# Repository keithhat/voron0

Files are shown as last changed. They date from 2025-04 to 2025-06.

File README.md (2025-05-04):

# voron0
This tracks my Voron 0 build.
This was originally a Siboor 0.2 r1 kit (Aug2023) with ABS printed parts. I bought of AliExpress from official Siboor retailer.
Having time again I'd see price bying from siboor directly to choose different colours.

# Main Info
* http://192.168.7.60/#/ (Ethernet)
	* WiFi 2.4GHz: http://192.168.7.61/#/
* Login:
	* username: fly
	* default password: mellow
* I bought this kit: https://www.aliexpress.com/item/1005005295642824.html
	* When purchased I got with Drafon HF Hotend and Red ABS parts for AUD 943.02 (with shipping).
	* As at 2025-05-01 it is: AUD 645.39 with no ABS and TZ-V6-2.0 (if wanted second...)
* Siboor has a collection of useful links: https://docs.siboor.com/welcome-to-siboor/friendly-links

# Notes
* Do NOT do full apt upgrade on console.
	* I initially broke my Siboor image doing this, I did force some which may have been kernal.
	* I got everything back using Gemini images and some sample Siboor files.
	* Updating through the mainsail interface was ok, including plugins. Some had path clashes that were easily resolved.
* The polarity of at least the extruder fan is important.
* My extruder was skipping when initially tuning, ended up being some broken filament in heatbreak. Disassembled and used a tool to help extract
* It was originally not clear to me, but the z-axis should be configured so toolhead is at 0.0 for correct printing location. (I originally had bottom as 0 and this at 120).

# Build Info
## Mechanical Assembly
* The mechanical build largely went well following the PDF manuals.
	* As this was a 0.2r1 kit some mod 'patches' were not fully covered.
* Main Manuals and Notes during mechanical assembly (in assembly folder):
	* [BuildNotes.md](assembly/BuildNotes.md) these are verbose notes /ideas while mechically building device
	* 0 Keith Notes.txt - this was intended as concise patches to readme and assembly manual
	* 1 README with deltas to official was originally from: https://github.com/Lzhikai/SIBOOR-Voron-0.2/blob/main/supplementary/README.md
  	* 2 Official 0.2 Assembly Manual was originlly from: https://github.com/VoronDesign/Voron-0/blob/Voron0.2/Manuals/VORON_V0.2_Assembly_Manual.pdf
  	* 3 Siboor Supplementary with info on Motors and Feet was originally from: https://github.com/Lzhikai/SIBOOR-Voron-0.2/blob/main/supplementary/SIBOOR%20V0.2%20Supplementary%20Manual.pdf
  	* 4 Siboor Supplementary with info on Wiring / Motors was originally from: https://github.com/Lzhikai/SIBOOR-Voron-0.2/blob/main/supplementary/SIBOOR0.2-supplementary.pdf
  	* 5 Siboor Upgrades was originally from: https://github.com/Lzhikai/SIBOOR-Voron-0.2/blob/main/supplementary/SIBOOR%200.2%20R0%20Upgrade%20R1%20Guide.pdf
 * Other Info:
  	* Siboor V0.2 Bom: https://github.com/Lzhikai/SIBOOR-Voron-0.2/blob/main/BOM.md
	* Root Project from QR Code: https://github.com/Lzhikai/siboor-voron/tree/main/Voron-0.2
* During assembly I originally missed the rear-right foot with bowden collet and run-out sensor.
	* This was created from the Siboor screenshot and required hardware in [RearRightFoot.jpg](images/R1_Rear_Right_Foot/RearRightFoot.jpg) (I only used 1 M2x10)
* The ADX345 accelerometer mounting was eventually found at end of "assembly/4 SIBOOR0.2-supplementary.pdf".
	* I had previouslly used longer bolts and attempt to mount to front of toolhead.
## Electrical
My extruder fan was not originally working. This was tracked to a polarity issue into the fan cable. These cannot be swapped.

## FW
(!)Do not do arbitrary system udpates for gemini board. Updating through mainsail interface was ok though.
Flashing fimware main indicate success and failure; this was found to be ok but confirmed through dfinding id

# Current Main Components
* Kirigami Bed
	* Has 8 RGB LED neopixel in logo
* Phaetus Dragon HF Hotend
* Gemini v3 mainboard
* V0 Umbilical
	* This is fairly stiff; a CAM bus or USB equivalent think would be useful in future

# Guides - Assembly, FW and Tuning
## General
* Siboor v0.2 r1 Aug: https://docs.siboor.com/siboor-0.2-r1-aug
	* Initial Startup and Wiring: https://docs.siboor.com/siboor-0.2-r1-aug/the-build/initial-startup
	* Mods to vanilla: https://docs.siboor.com/siboor-0.2-r1-aug/the-build/assembly-manual
* Gemini v3:
	* Image: https://mellow.klipper.cn/en/docs/ResDownload/system-img/fly-Gemini/?persistLocale=true
	* General: https://mellow-3d.github.io/fly-gemini_v3_general.html
	* Fan: https://mellow.klipper.cn/en/docs/ProductDoc/MainBoard/fly-gemini/fly-gemini-v3/fan/
* Voron: https://docs.vorondesign.com/build/software/

## Tuning and Initial Setup
This explicitly calls out some sections
* I missed it originally, but want to end up having z=0 (z0) being where the toolhead needs to be to touch plate and be ready for printing. We adjust Z switch so this is true.
	* See https://docs.vorondesign.com/build/startup/#stepper-motor-check and matching video: https://www.youtube.com/watch?v=wXYruV6QdDQ$t=1700
* Moving, homing, estep, PID: https://docs.vorondesign.com/build/startup/
	* Sensorless Homing: https://docs.vorondesign.com/tuning/sensorless.html
	* A video of these is: https://www.youtube.com/watch?v=wXYruV6QdDQ
* Klipper Common Errors: https://docs.vorondesign.com/community/troubleshooting/eddie/klipper_common_errors.html

## Sample Configus
* Siboor Voron 0.2 Aug: https://github.com/Lzhikai/SIBOOR-Voron-0.2-AUG/blob/main/printer.cfg

## Neopixel
0.2 Kirigami bed has a neopixel LED that can have effects. This can be used with 2xLED strips as 'Disco on a Stick' with wiring shown at [DaisyChain Neopixel RGBs](images/02_LED_Wiring/Multiple_RGBs.jpg)

### LED effects
* https://github.com/julianschill/klipper-led_effect
* https://docs.siboor.com/other-products/led-effect-notes/configuring-the-effects
* https://docs.siboor.com/other-products/led-effect-notes/advanced-effect-layer-blending

### Various Sample Effects
* https://gist.github.com/bistory/08e279ebda4d5cd2521dfe1add09dab4
* https://pastebin.com/GBzkNXcq
* https://pastebin.com/pv8M4huD
* https://github.com/julianschill/klipper-led_effect/blob/master/examples/Voron_Stealthburner/stealthburner_led_effects_3_leds.cfg

## Ultimaker Cura Integration
* I followed the guide at: [3 Siboor v0.2 Supplementary Manual](https://github.com/Lzhikai/SIBOOR-Voron-0.2/blob/main/supplementary/SIBOOR%20V0.2%20Supplementary%20Manual.pdf)
	* Same info in [4 Siboor0.2-Supplementary.pdf](https://github.com/Lzhikai/SIBOOR-Voron-0.2/blob/main/supplementary/SIBOOR0.2-supplementary.pdf)

## Unsure if used:
* https://www.klipper3d.org/Config_Reference.html

# Additional Purchases:

## Parts for physical assembly (also in [BuildNotes.md](assembly/BuildNotes.md))
* Isopropyl alchohol
* WD40 White Lithium Greece (spray can)
    * I used as lubricate for linear rails and screw
* Permatex White Lithium Grease - 80345 for bearings
    * For print head bearings
* Locktight Blue for grub screws
* Super glue for print head nut
    * I had 2 part 5min eproxy
* Cable cutter and stripper
* JST XH connector tool - at least for hotend to Umbiligal PCB
* Optional:
    * Cable management stickies

## Tools post-assembly
The Dragon HF seemed to be missing some additional tools in full kit; ended up getting the following to help
I bought following:
* Open Ended Mini Spanners: https://www.amazon.com.au/dp/B0DBY93B7Q 			AUD 14.98 	Set (4mm, 4.5, 5, 5.5, 6, 7, 8, 9, 10, 11)
    * These worked for removing nozzel from Dragon HF, but was relatively thick for disassembly heatbreak from heat-block.
* Hex Wrench for Dragon HF heat-block (1.27mm):
	* https://www.ebay.com.au/itm/196192220714 AUD 24.88 for Set (0.9, 1.27, 1.3, 1.5, 2.0)
	* https://www.ebay.com.au/itm/134291755243 AUD 3.10 single 1.27mm
* Hex multi-tool to help with Hotend: https://www.amazon.com.au/dp/B0DSBQDLFP 	AUD 11.89 	Spanner: (6, 7, 8, 10,20), Hex Tool: (M2.5, M2, M3, M4), Copper Wire Brush
	* Got to help have a thinner spanner for Dragon HF disassembly - unblocked before needing to disassemble.
* Filament unblock tool (when nozel removed): https://www.aliexpress.com/item/1005002948629438.html 	AUD 2.95
	* I made a seperate heatbreak and heat block that could be connected to umbilical and moved from printer to help unblock.
		* Heater Block: https://www.aliexpress.com/item/1005005038625574.html 	AU 8.99 	Up to 500deg. Missing silicon sock, I got the wrong one.
* Nozzle Needless:
	* https://www.aliexpress.com/item/1005004227280655.html AUD 4.09 	(0.2 and 0.5)
* Anti-Static Tweezer set: https://www.aliexpress.com/item/1005007425589207.html 	AU 4.59

# Additional Parts
## General
These can be ued with several of below
* I bought several hardened steel nozels for different sizes and abrasive materials.:
	* https://www.aliexpress.com/item/1005001620042630.html 	AUD 4.14  	I got pairs on: (0.2, 0.4, 0.6)
* Drive Gear with Hardended Steel gears - have NOT yet used this for gears (arrived after re-assembling mini Stealthburner)
	* https://www.aliexpress.com/item/1005007929025658.html 	AU 7.39 	Intended as spare 50T gear and abrasiev filamenets.
* Adapter for screen USB Cable
	* This seemed tight against sides; didn't want to damage the screen cable so got something else to prolong life.
	* Tried a few 90deg adapters but either blocked ports or didn't have clearance.
	* Currently using a USB A 30cm extension cable: https://www.ebay.com.au/itm/135236859084 AU 4.95
* Small Camera:
	* USB 'RPI 3 Model B 640x480' https://www.amazon.com.au/dp/B09KHHN8B3 	AU 13.26 Not yet working; unsure if HW/SW/Drivers

## Parts for Dragon HF Hotend abrasive/replacement
These are not yet used, arrived too late. 
TODO: Need silicon cover. This is WRONG for Phaetus Dragon HF: https://www.aliexpress.com/item/1005005886011113.html 	AU 5.79
TODO: Need cool zone? Possibly something that can be shared with EnderNG
* I made a hotend that could be used to unblock hotend or nozels (think 3rd party Dragon HF):
	* 50W 24V thermistor / heaterset: https://www.aliexpress.com/item/32967546419.html 	AU 5.39
	* HF Heatbrewak: https://www.aliexpress.com/item/1005006869637598.html 	AU 23.79

## Replacement Hotend
A cheaper hotend for abrasive seems useful. Also allows using if Dragon blocked.
TODO: Confirm can use above hardened steel nozzels
TODO: Make up as drop-in for Dragon HF; mini stealthburner, then Dragon Burner
* I later bought a TZ-V6 2.0 Hotend - 35mm3/s
	* 60W V6: https://www.aliexpress.com/item/1005006417172044.html 	AU35.19. TBC if ok for abrasive.
		* Nozzle: SKD11, hardness: HRC60 - TBC if takes above V6 hardened stell (this looked smaller.)

## Dragon Burner
The Dragon Burner seems to be better reviewed, especially for PLA. Also would like a filament cutter (for box turtle) and nozzle probe for correct z-offset.
Home is: * Dragon Burner v8 Home: https://github.com/chirpy2605/voron/blob/main/V0/Dragon_Burner/README.md

### Bought Parts
* 1x 3010 24V 			https://www.aliexpress.com/item/1005002857100082.html 	AU 13.89 x1
* 2x 4010 Blower 24V 	https://www.aliexpress.com/item/32799324058.html 		AU 9.49 x2
* Orbiter v2.5 Extruder: https://www.aliexpress.com/item/1005007653572332.html 	AU 79.18
* Logo NeoPixel: https://www.aliexpress.com/item/1005006046634379.html 	AU 11.79 	(looks to have sockers already) + 2 LEDs
	* NeoPixel DIY: https://www.aliexpress.com/item/1005007646205279.htm 	AU 6.09 	<- Unsure if would be better than above. Got both to check.
* RGA Sequins: https://www.aliexpress.com/item/1005006023213341.html 	AU 5.62 (4 LEDs)
	* Neopixel Alternative: https://www.aliexpress.com/item/1005006220336798.htm 	AU 5.79 	<- I got both, thought this was neopixel above normal RGB

## Purchases but not necessarily used:
These maybe used on my Ender3 v2 to NG upgrade instead (for larger build volume). Plan to do that AFTER the v0.2 is working so have something working at all times.
* Funssor Ender 3 NG Conversion Kit: https://www.aliexpress.com/item/1005006191089001.html 	AU 188.98 motion and electronics
	* Note bought in 2024 prior to offical release. Maybe newer versions now eg : https://www.aliexpress.com/item/1005007822628611.html Ender NG v1.2 for 290.99 / 326.69 wuth motors
* Klipper expansion board - may need for lights: https://www.aliexpress.com/item/1005005777656355.html 	AU24.99
* Klicky Kit for bed levelling: https://www.aliexpress.com/item/1005005467101449.html 	AU 7.19 	Bought in 2024, maybe better optiosn now
* Nevermore v6 DUO Cabon Filters for Voron: https://www.aliexpress.com/item/1005005621338360.html 	AU 36.05 for 2
* PEI + Smooth PEO Build Plate: https://www.aliexpress.com/item/1005006950525967.html 	AU 11.37
* RGB LEDs: https://www.aliexpress.com/item/1005007075886697.html 	AUD 17.27 for 2x158mm
* Belt Tensionmeter: https://www.aliexpress.com/item/1005006724674386.html 	AU 12.20 (I used guitar tuner while initially building)
* ADXL345 3 Axis Acceleration Module: https://www.aliexpress.com/item/32452794842.html 	AU 5.41 (think kit had some too)
* Filament Run-out sensor: https://www.aliexpress.com/item/32917462715.html 	AU 3.35
* PTFE Tube https://www.aliexpress.com/item/1005004969503645.html 	AU 7.50 for 2m with cutter
* 10ml 243 Loctite: AUD 4.42
* G10 FR4 FibreGlass Sheet (Green PCB Material):
	* Single Sided Copper: https://www.aliexpress.com/item/1005006103130312.html 	AU 4.39 for 120x180 - I have 20x30 for 9.74
	* AU 14.19 for 235x235x1.5mm

# Interesting parts that may help in future
 * [NoDropNuts](https://mods.vorondesign.com/details/XGjXJC3VQU76EBYB7Yg) look interesting
 * [Snap in M3 Nuts for 1515](https://www.printables.com/model/410126-snap-in-m3-nuts-for-makerbeam-xl-1515) - ie for Nevermore

# Future Thoughts
These are tracked in [Future.md](future.md)

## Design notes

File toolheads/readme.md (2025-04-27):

This is tracking my ideas for hotends.
There maybe other info at: https://3dprintersforants.com/

Rough plan is:
	- Have a Dragpn HF in Mini Stealth burner.
		- Want a second Hotend for abrasive materials - also handle blocks
		- MAY want additional parts to help with Dragon HF clogs - think had snapped filament cause this at start

Mini StealthBurner - Default Toolhead

Dragon Burner:
	- https://github.com/chirpy2605/voron/tree/main/V0/Dragon_Burner
		- v8 was defined for Voron 0.2
	- Bom (Extracted)
		- FANS:
			- Part Cooling: 2x 4010 24V blower fans
				- Recommended: https://www.aliexpress.com/item/32799324058.html 	(24V Hydraulic 2PIN) AUD 5.05
			- Hotend Cooling: 1x 3010 24V
				- Recommended: https://www.aliexpress.com/item/1005002857100082.html ( 24V Sleeve 2PIN) AUD $ 12.79
		- LEDs:
			- 3x LEDs for lgoo and nozzle lights (optional)
				- Can be a mixture of NeoPixels and/or Sequins (nozzle??)
				- Support has been added for either standard Neopixels or Sequins for the nozzle LEDs, Neopixels, Sequins and RainbowBarf for the Logo LED.
				- Links I found:
					- https://www.aliexpress.com/item/1005007646205279.html AUD 1.59 (need to solder/crimp myself)
					- https://www.aliexpress.com/item/1005006046634379.htm AUD 10.59 looks socketed prepared for StealthBurner
					- Sequins: https://www.aliexpress.com/item/1005006023213341.html AUD 1.59 - DIY
					- Neopixel Sequins: https://www.aliexpress.com/item/1005006220336798.html AUD 1.83
		Dragon SF and HF
		Dragon + Volcano (Rapido HF mount)
		Dragonfly BMO
		Dragonfly BMS (7 fin)
		Revo Voron
		Rapido HF
		NF Crazy
		Creality Spider Pro
		Bambu Labs X1C
		TaiChi
		E3D V6 Groove Mount
		Red Lizard K1 Pro (Dragon mount)
		Red Lizard K1 UHF (Rapido HF mount)
		Dragon Ace HF (with spacer use the Rapido HF mount, without spacer use the Dragon Ace HF mount)
		Phaetus NeXt G HF (Dragon mount)
		Phaetus NeXt G UHF (Rapido HF mount)
	- Extruder:
		Extruder support:
		E3D Roto Vitamins (use the Sherpa Mini hotend mount)
		LGX Lite (use the Sherpa Mini hotend mount)
		Sherpa Mini
		Sherpa Micro
		Sailfin/Sharkfin
		Orbiter v1.5
		Orbiter v2
		Vz-HextrudORT (Uses the LGX Lite extruder mount and Sherpa Mini hotend mount)
		Double Folded Ascender
		RoundTrip (Gears from the LGX Lite, TBG Lite, Orbiter v1.5, Orbiter v2)
		Galileo v2 Standalone (G2SA) with specific mounts for Sherpa Mini and Orbiter v2 mount hole configurations
		Wristwatch BMG and G2 use the Orbiter v2 hotend mounts
		Papilio Lite (Paplite) extruder (use Sherpa Mini mount)
	- Probes:
		- SlideSwipe magnetic probe support: https://github.com/chestwood96/SlideSwipe - likley start with: https://github.com/chestwood96/SlideSwipe/blob/master/Alternative_Mounts/FrontCowlingMount/README.md
		- (Un)Klicky Probe support: https://github.com/jlas1/Klicky-Probe/tree/main/Printers/Voron/v0 (also read https://github.com/T4KUUY4/Voron-Stuff/tree/main/KlickyProbeZoffset)
			- https://github.com/jlas1/Klicky-Probe/tree/main/Printers/Voron/v0#integrated-cowling-v01
			- https://github.com/jlas1/Klicky-Probe/tree/main/Probes/KlickyNG
		- ZeroClick probe support: Inspired by Clikcy but for small printers: https://github.com/zruncho3d/ZeroClick
		- Think also Tap and Boop in mounts
	- Mounts:
		- Extruder and PCB Mounts: https://github.com/chirpy2605/voron/tree/main/general/PCB_Mounts
		- Alternative Mounts: Mounts are available
	- Extra:
		- ADXL345 front mount
		- Heatsink thermistor support on most hotend mounts
		- Neopixel support (nozzle and logo)
		- Adafruit Sequin support (nozzle and logo)
		- [Lab4450](Shop - RGB Neopixel Sequins for Voron Mini SB - Lab4450.com) Neopixel Sequin support (nozzle and logo)
			- https://lab4450.com/product/rgb-neopixel-sequins/ EU 2.00
			- https://github.com/julianschill/klipper-led_effect

Noet:
	- Avoid XoL

Want:
	- Dragon HF
	- V6 PZ
	- Orbiter v2.5++

Stetech:
	- Filament Cutter (for AMS)
	- Probe:
		- TAP: https://github.com/chirpy2605/voron/tree/main/general/Alternative_Voron_Mounts/Modified_Mounts/Tap
	- Vooron Revo (ideally with PZ)
		- MAYBE easier to clear clogs;
			- Possibly something else to heatup outside of printer

Future:
	-CAM Bus

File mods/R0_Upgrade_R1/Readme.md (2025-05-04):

# README.MD

These are the Siboor R1 STL Updates
They were downloaded from: https://github.com/Lzhikai/SIBOOR-Voron-0.2/tree/main/supplementary/R0_Upgrade_R1-STL

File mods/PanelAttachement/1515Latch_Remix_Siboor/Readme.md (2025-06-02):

This is from: https://www.printables.com/model/512829-voron-0-filament-latch-remix-for-no-drop-nuts-sibo/files
	- It is remixed of the LDO motors version https://www.printables.com/model/172427-voron-01-filament-latch-1515-extrusion which was based off 2.4 2020 version: https://github.com/richardjm/voron-parts/tree/main/voron-2.4/FilamentLatch

Note:
	- There are two versions here:
		- Short lengths - work with NUT in Siboor/Makerbeam 
		- Stub for no drop nuts
	- Use two per panel edge so 8 for left and 8 for right
		- Maybe spacers for middle of each
	- Door cam ise as a latch

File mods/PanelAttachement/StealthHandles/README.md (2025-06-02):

Source: https://mods.vorondesign.com/details/GHaVestXfFM0svkcJRpk2A

# V0 Stealth Handles

Stealthy and stylish handles for your Voron V0

These handles replace the top center panel clips, and fasten with M3x12 screws.

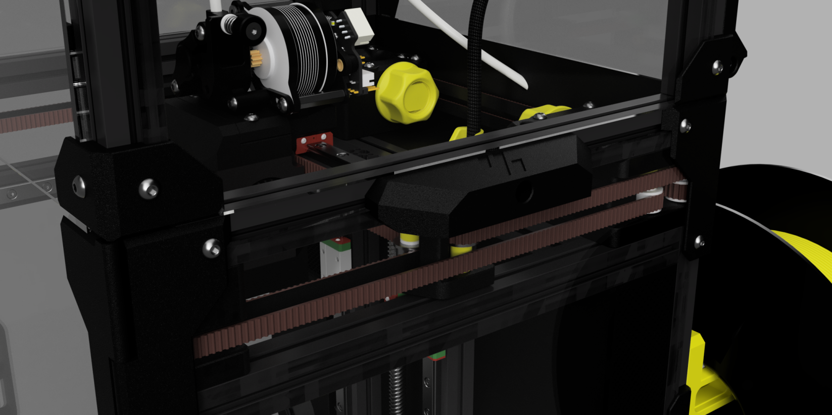
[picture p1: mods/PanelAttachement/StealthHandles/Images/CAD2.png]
CAD2


## Printing

The STL files are already oriented for printing.  No supports are required.  Yes, they print at a 45 degree angle, for some extra strength.

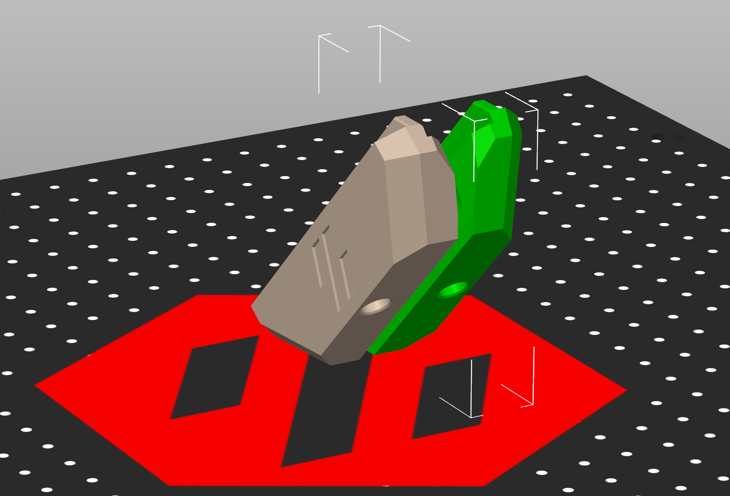
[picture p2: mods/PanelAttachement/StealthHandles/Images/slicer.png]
Slicer


## Changelog

2023-08-24 - Slim down the tabs by 0.2mm for a better fit with some extrusions.

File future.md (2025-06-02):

# Backlog of tasks

This is a backlog of tasks I'd like to improve. It was started after initial mechanical assembly.

# Current Status

## Final setup before doing generic prints

* Calibration Prints
  * cube https://docs.siboor.com/siboor-0.2-r1-aug/the-build/slicer-setup#slice-the-3d-model
  * Initial observations:
      * First layer indicated some issues with oozing; at leat the white filament. Moving from purge line; and first layer
        * Think this is mainly retraction; think a stringing test to help set
      * >>> Have seen layer shits; not always reproduced so see if cause <<< Belt tension, speed etc
      * Klipper console log showed some details - unknown command:
        * Unknown Command:
        *   EXCLUDE_OBJECT_DEFINE - at start
        *   EXCLUDE_OBJECT_START - lots of pairs
        *   EXCLUDE_OBJECT_END 0 lost of pairs
        * Popup at end of Job: Move out of Range: 230 230 36 [7355.028]
      * Some lines shown; seem consistent (for same job); are around end of z etc so maybe not just fixed x cm issues.
      * Annoying; sometimes fails saying neded to home first (after pre-heats bed)
        * This MAYBE intermittent?
  * Assume Will Need:
    * Look for a spool holder incase caused layer shifts - MAYVE poorly mounted originally (using E3 for now)
    * Look at flow rates for material - load filament FAST for ABS resulted in skips towards the end
    * Temperature Tower
    * Retraction Distance - Is this related to oozing??
    * First Layer??
    * Max Dimensions; especially Z and no shifts
    * Anything to help tune acceleration?
  * Maybe more at: https://docs.siboor.com/siboor-0.2-r1-aug/tuning-guides (some of these are below in stretch)
  * Teching Tech or makers muse likely have others; retraction, overhangs etc
* Move printer to next to ender3

## Nice to Have
* Filament runout sensor - from foot
* Look at accelerometer and input shaping.
  * Resonances: https://docs.siboor.com/siboor-0.2-r1-aug/tuning-guides/measuring-resonances
* Check if need to tune: Pressure Advance, Smooth Time
  * Pressure Advance: https://docs.siboor.com/siboor-0.2-r1-aug/tuning-guides/pressure-advance
  * Sameple videos: https://www.youtube.com/watch?v=deqJTNmnVyc  https://www.youtube.com/watch?v=LVp15eGXwm0

## Assistance for maintenance
* Case clips for panel quick attach/detach.
  * Several potential options; check all for V0.2 rather than V2.4 etc
    * Snap Latch for 1515: https://www.printables.com/model/172427-voron-01-filament-latch-1515-extrusion
      * As have M3 nuts MAYBE look at these. Unsure if other remixes etc
    * [FT Panel Clips for Voron V0/V0.1/V0.2] (https://www.printables.com/model/933648-ft-panel-clips-for-voron-v0v01v02) Only negative is key isn't flush
      * Alternative with same idea; https://github.com/KayosMaker/1515PanelClips (based on Annex but no longer skeletonized)
    * Potentially best magnet idea: https://www.printables.com/model/435407-voron-magnetic-panel-clips/comments
      * Unsure if need something else for doors
    * Zero Panels: https://github.com/zruncho3d/ZeroPanels
      * v3 Has tape mainly to keep alignment; potentially would like a version 2 without?
      * Some remix: https://github.com/adooze/ZeroPanels_for_Stock_V0.2
    * Excessively Magnetic Panel Mod https://www.reddit.com/r/VORONDesign/comments/1ccbihw/the_excessively_magnetic_panel_mod_emp_is_now_in/ / 
      * Needs 236x 6x3mm Magents, 8x M3x8 screens, 69xNits and VHB tape
      * Similar (unsure what are best):
        * https://github.com/VoronDesign/VoronUsers/tree/main/printer_mods/bobbleheed/Magnetic_Panels / https://mods.vorondesign.com/details/xQAsIUzijkbXU2yXrRKdXg
* Door handle fix - I'm ok to screw through front panel
  * Randome link: https://mods.vorondesign.com/details/mbzWlsb9PXA54FhWXtRCQ
* Add panels for dust etc
* MAYBE a nozzle cleaner? Lots of ozzing atm. Especially want if using nozzle probe
* Belt Tesnsion checking
  * https://github.com/Diyshift/3D-Printer/tree/main/GT2%20Belt%20Tension%20Meter
    * Need Spring and Piano wiring for correction tension
    * Video of demo: https://www.youtube.com/watch?v=AmgCqy7FisE
    * Link has tension guidlines: 1.9 for Voron 0. When printhead centered (and motors active)

## MVP Completion
* Look at process to apply for serial.

## Stretch

* LED Strips and possibly affects (if RGB)
    * Wiring: https://docs.siboor.com/siboor-0.2-r1-aug/faq-oct-3 
    * https://docs.siboor.com/other-products/led-effect-notes
    * https://docs.siboor.com/other-products/rgb-pcb-light
    * Also some Daylight STLs to mount
* Klipper LED as status - Something for Printing (percentage); loading job? Pause
    * Really want:
      * toolhead neopixel; so can indicate temperate
      * Enclosure LEDs; help show status?
* Camera - mount on top of z extruction.
    * I bought: https://www.amazon.com.au/dp/B09KHHN8B3
      * Look at designing own back mount to replace clip; USB strain relieft MAY need looking at; don't want to resolder anything when swap
      * I broke the retraction (spring flew out).

## Nice to improve

* Can extruder fan be controlled? Think also called hotend fan. Mainly for me being in same room :)
    * Ideally off unless extruder > say 40deg. Allows machine to be quieter / always on.
    * According to: https://docs.siboor.com/siboor-0.2-r1-aug/the-build/initial-startup-checks the Hotend fan cannot be controlled.
    * Any spare switch we can use to control?
    * https://docs.vorondesign.com/build/startup/#pid-tune-bed--hotend says Parts cooling to 25% can be done with: M106 S64
    * Eg: SET_FAN_SPEED FAN=Nevermore SPEED=0.7
    * Fly_Gemini_v3 defines:
        * FAN0=PC6,
        * FAN1=PC7,
* Modest Mesh; maybe several options eg: https://www.printables.com/model/407822-voron-v0-modesty-mesh
* Carry Handle

* What is the MCU LED - has the Kirigami LED replaced this?
* Nevermore chamber filter - to help with ABS fumes as know will be in confined space
* Z-Stop - ideally Nozel probe
    * Prefer probe bed accuratly than assume offset - potentially max height issues though. Good to understand why v0.2 moved to bottom?
    * This looks simple/cheap - doesn't allow for different beds though: https://github.com/Polar-Ted/STL-Files/tree/main/V0.1_Its_Not_a_Sexbolt_switch
        * Video is at: https://www.youtube.com/watch?v=bdxmqTDDsMM
    * Expect some options especially if change to DragonBurner - this would allow for differnt beds too.
    * There are now lots of new options possibly for bed leveling/mesh:
      * Beacon/Cartographer (original)
      * Eddy
      * Tap -> Moves entire toolhead so less rigid; BUT has both bed and nozzle.
      * Klacky? - look at
        - Unsure of nap that nozzle pushed on button next to bed. If this then one it picks up probe temporarily
      * BLTough ? unsure if still useful

* Ensure idler cam locks work well with printer hat
* Check toolhead is ok with PLA, may need better cooling. Think Dragon Burner useful and helps with some other options (filament cutter, maybe probe)
    * Can explore other options including CAM controlled for more flexible cambling
    * Consider adding LED lights; I decided to NOT use in original mini StealthBurner build
    * Consider a filament cutter to allow AMS system such as armoured turtle, 8 track or ERCF v2.
    * Additional filament sensors (blocked?)

# Maintenance
* Belt Tension:: https://www.youtube.com/watch?v=AmgCqy7FisE

# Print Fixes / Upgrades
* AC input fix
* Fix door handle
* Carry Handles
* Panel clips for quick removal
    * Zero Panels; have v3 that has tape PLUS foam. Will click onto frame so tape doesn't need to be too strong.
        * Worth looking for earlier versions which think skip tape; maybe slide on corerns
* Alternative filament path
* Camera mount

# Future Mods:
- Hat access filament > short path
    - Filament run-out senseor
- Fan for fumes and bed heting.
- Privacy for rear of chamber
- Protector behind screen?
- Magentic side mounts?
- Shorter HAT to fit in cube
- Unsure: Filament runout sensor
- Cam Locks > Larger hex wrench??. Maybe better options
- I MAY have an expander; if so look at installing (possibly need for LEDs):
    - https://github.com/Lzhikai/SIBOOR-Voron-0.2/blob/main/expander/README.md

# Useful Ideas for storing tools:
* Container hold set of smaller wrench; ideally rotatable like one of the screwdrivers I have.
  * MAYBE want a flat cotiner; tbc
* Something to store the hex driver sets I have
* Something to hold collection of alan keys; sort between printers.
* Something to hold collection of flat cheapper spanners; sort between printers

# Consider Buying Addons
* Alternative beds; ensure have something for each type; PLA, ABS, PETG
  * Glass (Tile?)
  * G10/FR4 PCB material as Bed
* INDX looks interesting, expect to fit 4x toolchangers in V0. Can be shared with EnderNG etc. Think LATE 2025 but monitor as closer
  * Especially if can support/requires CAM or USB extension. Can start replacing other toolheads earlier.
* Do up V6 drop-in could be good for replacements (replaced by above) - mini steath burner then dragon burner.
  * Didn't notice a V6 in https://github.com/Lzhikai/SIBOOR-Voron-0.2/tree/main/STL/Toolheads%EF%BC%88%E5%B7%A5%E5%85%B7%E5%A4%B4%EF%BC%89/Hotend_Mounts
* Box Turner AWS - allow filamenet swaps after filament cutter
  * May need filamenet run-out sensors etc
* Consider CAM or USB version to toolhead vs this V0 Umbilical solution - maybe add to ender NG too for more mainline support/shared data.
* Maybe replace Fly-Gemini-V3 to RPI4 and generic with CAM support. Allow mainline klipper??

* Randome Modded V0.2 for ideas:
  * https://forum.vorondesign.com/threads/my-voron-0-2.1587/

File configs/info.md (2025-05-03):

# Klipper setup / config / tuning

# Config Files 
I'm still learning klipper so there maybe better ways to backup files.
This has that information with a combination of where to place them.

## Paths

These paths are using the Gemini board FW locations
* /home/fly/printer_data/config/
	* printer.cfg is the main one that references everything
	* boards/FLY_GEMINI_V3.cfg defines aliases for various pins so can have generic references in other config files
	* V0Display.cfg configures the USB display
	* fly_macros.cfg defines some gcode macros including the homing functions.
	* mainsail.cfg is a simlink to /home/fly/mainsail-config/client.cfg
	* fluidd.cfg is a simlink to /home/fly/fluidd-config/client.cfg

## Extras
* The LEDs:
	* klipper/klippy/extras/led_effect.py is a simlink to /home/fly/klipper-led_effect/src/led_effect.py

# Tuning Notes
## Do STEPPER_BUZZ for correct directions
* The STEPPER_BUZZ (and then homing down) was useful for me to confirm z-axis. I'd assumed printing location should be 120 but this really should be 0.0.
	* STEPPER_BUZZ https://docs.vorondesign.com/build/startup/#stepper-motor-check and matching video: https://www.youtube.com/watch?v=wXYruV6QdDQ$t=1700
* ALSO note that homing direction can be set in config file - confirm these two.

## Z Axis:
* Z Calibration
	* Home - will go down to bottom (max) then move back up to 30 (soem distance from nozel).
	* From https://docs.vorondesign.com/build/startup/#z-endstop-location-v0 run Z_ENDSTOP_CALIBRATE to tune Z0 to nozzle and setup position_endstop.
		* Nozzle cold with paper; as thermal expansion is 100um ~ paper
		* Video of similar is at: https://www.youtube.com/watch?v=wXYruV6QdDQ&t=2110
* Bed Levelling:
	* After homing can run BED_SCREWS_ADJUST
		* Manual is at: https://docs.vorondesign.com/build/startup/#bed-leveling
		* Video is at: https://www.youtube.com/watch?v=wXYruV6QdDQ&t=2480
	* After levelling, redo the z-calibration (Z_ENDSTOP_CALIBRATE) to ensure probe is correct
* The following siboor manual may also be useful: https://docs.siboor.com/siboor-0.2-r1-aug/the-build/initial-startup-checks#calibrate-the-z0-position
* Note: I repeated when at PLA temps BED 60, Extruder 200 incase warming.

# Pluggins
## Neopixel LEDs - ie BED Logo
Installed from: https://docs.siboor.com/other-products/led-effect-notes/installing-led-effects-software

```
cd ~
git clone https://github.com/julianschill/klipper-led_effect.git
cd klipper-led_effect
./install-led_effect.sh
```

## Crowsnest for USB camera
* It seems crowsnest deprecated MJPEG-streamer. Repo is at:  https://github.com/mainsail-crew/crowsnest
	* These command were from: https://www.youtube.com/watch?v=7A4wIKLQQoM&ab_channel=PrintsLeo3D
		* My image already had a ~/crowsnest so I commented out the first few lines
		```
		# cd ~
		# git clone https://github.com/mainsail-crew/crowsnest.git
		cd ~/crowsnest
		sudo make install
		# This did some apt updates - I had to do Armbian fix below
		```
	* Looking at error log (/home/fly/printer_data/logs/crowsnest.log) allowed me to setup crowsnest.conf - was using incorrect device
	* Needed to restart crowsnest then klipper.
	* Note: Only gettig around 5fps

# Apt Fixes

## Armbian key issues

I had the following message during apt update:
```
sudo apt update
Get:1 https://github.armbian.com/configng stable InRelease [3,992 B]
Err:1 https://github.armbian.com/configng stable InRelease
  The following signatures couldn't be verified because the public key is not available: NO_PUBKEY 93D6889F9F0E78D5
Hit:2 http://repo.jing.rocks/armbian-apt bullseye InRelease
Hit:3 https://mirrors.tuna.tsinghua.edu.cn/debian bullseye InRelease
Hit:4 https://mirrors.tuna.tsinghua.edu.cn/debian bullseye-updates InRelease
Hit:5 https://mirrors.tuna.tsinghua.edu.cn/debian bullseye-backports InRelease
Hit:6 https://mirrors.tuna.tsinghua.edu.cn/debian-security bullseye-security InRelease
Reading package lists... Done
W: GPG error: https://github.armbian.com/configng stable InRelease: The following signatures couldn't be verified because the public key is not available: NO_PUBKEY 93D6889F9F0E78D5
E: The repository 'https://github.armbian.com/configng stable InRelease' is not signed.
N: Updating from such a repository can't be done securely, and is therefore disabled by default.
N: See apt-secure(8) manpage for repository creation and user configuration details.
```

This was resolved by adding a key (found these looking though foroms from above error)
```
sudo wget https://apt.armbian.com/armbian.key -O key
sudo gpg --dearmor < key | sudo tee /usr/share/keyrings/armbian.gpg > /dev/null
sudo chmod go+r /usr/share/keyrings/armbian.gpg
sudo echo "deb [arch=$(dpkg --print-architecture) signed-by=/usr/share/keyrings/armbian.gpg] http://apt.armbian.com $(lsb_release -cs) main  $(lsb_release -cs)-utils  $(lsb_release -cs)-desktop" | sudo tee /etc/apt/sources.list.d/armbian.list
sudo apt update
```

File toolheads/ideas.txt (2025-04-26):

This is tracking my ideas for hotends.
There maybe other info at: https://3dprintersforants.com/

Rough plan is:
	- Have a Dragpn HF in Mini Stealth burner.
		- Want a second Hotend for abrasive materials - also handle blocks
		- MAY want additional parts to help with Dragon HF clogs - think had snapped filament cause this at start

Mini StealthBurner - Default Toolhead

Dragon Burner:
	- https://github.com/chirpy2605/voron/tree/main/V0/Dragon_Burner
		- v8 was defined for Voron 0.2
	- FANS:
		- Part Cooling: 2x 4010 24V blower fans
			- Recommended: https://www.aliexpress.com/item/32799324058.html 	AUD 5.05
		- Hotend Cooling: 1x 3010 24V
			- Recommended: https://www.aliexpress.com/item/1005002857100082.html AUD $ 8.78

	- Hotends:
		Dragon SF and HF
		Dragon + Volcano (Rapido HF mount)
		Dragonfly BMO
		Dragonfly BMS (7 fin)
		Revo Voron
		Rapido HF
		NF Crazy
		Creality Spider Pro
		Bambu Labs X1C
		TaiChi
		E3D V6 Groove Mount
		Red Lizard K1 Pro (Dragon mount)
		Red Lizard K1 UHF (Rapido HF mount)
		Dragon Ace HF (with spacer use the Rapido HF mount, without spacer use the Dragon Ace HF mount)
		Phaetus NeXt G HF (Dragon mount)
		Phaetus NeXt G UHF (Rapido HF mount)
	- Extruder:
		Extruder support:
		E3D Roto Vitamins (use the Sherpa Mini hotend mount)
		LGX Lite (use the Sherpa Mini hotend mount)
		Sherpa Mini
		Sherpa Micro
		Sailfin/Sharkfin
		Orbiter v1.5
		Orbiter v2
		Vz-HextrudORT (Uses the LGX Lite extruder mount and Sherpa Mini hotend mount)
		Double Folded Ascender
		RoundTrip (Gears from the LGX Lite, TBG Lite, Orbiter v1.5, Orbiter v2)
		Galileo v2 Standalone (G2SA) with specific mounts for Sherpa Mini and Orbiter v2 mount hole configurations
		Wristwatch BMG and G2 use the Orbiter v2 hotend mounts
		Papilio Lite (Paplite) extruder (use Sherpa Mini mount)
	- Probes:
		- SlideSwipe magnetic probe support
		- (Un)Klicky Probe support
		- ZeroClick probe support
	- Extra:
		- ADXL345 front mount
		- Heatsink thermistor support on most hotend mounts
		- Neopixel support (nozzle and logo)
		- Adafruit Sequin support (nozzle and logo)
		- [Lab4450](Shop - RGB Neopixel Sequins for Voron Mini SB - Lab4450.com) Neopixel Sequin support (nozzle and logo)

Noet:
	- Avoid XoL

Want:
	- Dragon HF
	- V6 PZ
	- Orbiter v2.5++

Stetech:
	- Filament Cutter (for AMS)
	- Probe:
		- TAP: https://github.com/chirpy2605/voron/tree/main/general/Alternative_Voron_Mounts/Modified_Mounts/Tap
	- Vooron Revo (ideally with PZ)
		- MAYBE easier to clear clogs;
			- Possibly something else to heatup outside of printer

Future:
	-CAM Bus

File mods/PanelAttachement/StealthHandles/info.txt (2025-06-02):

From: https://www.printables.com/model/481575-voron-v0-stealth-handles

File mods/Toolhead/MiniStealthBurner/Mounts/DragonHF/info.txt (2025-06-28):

https://github.com/Lzhikai/SIBOOR-Voron-0.2/blob/main/STL/Toolheads%EF%BC%88%E5%B7%A5%E5%85%B7%E5%A4%B4%EF%BC%89/Hotend_Mounts/Fan_Saver/%5Ba%5D_FS_Hotend_Mount_Drag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

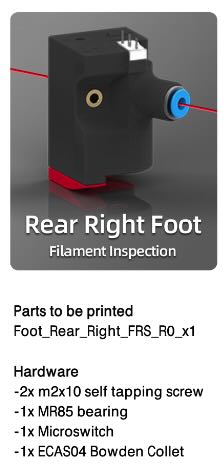
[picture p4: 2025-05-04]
images/R1_Rear_Right_Foot/RearRightFoot.jpg

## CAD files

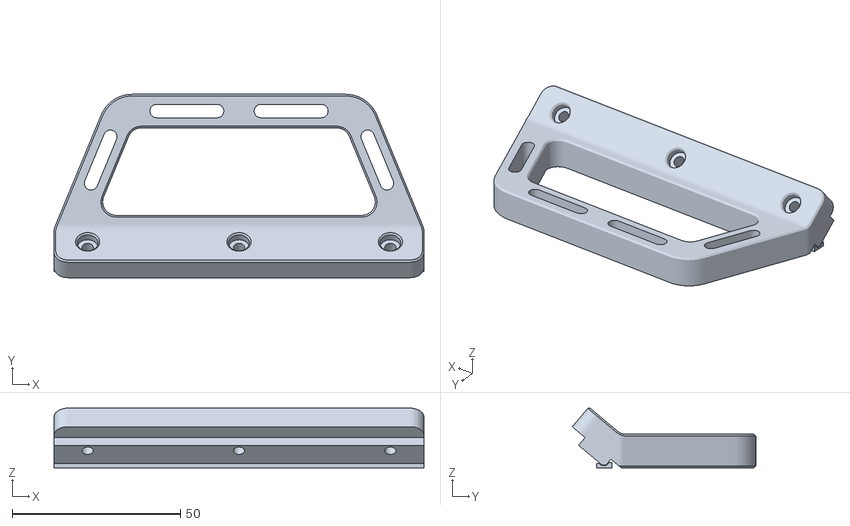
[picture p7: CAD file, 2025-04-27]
mods/Abandoned/CarryHandles/VORON 0 carrying handles.stl
110.0 x 54.6 x 17.8

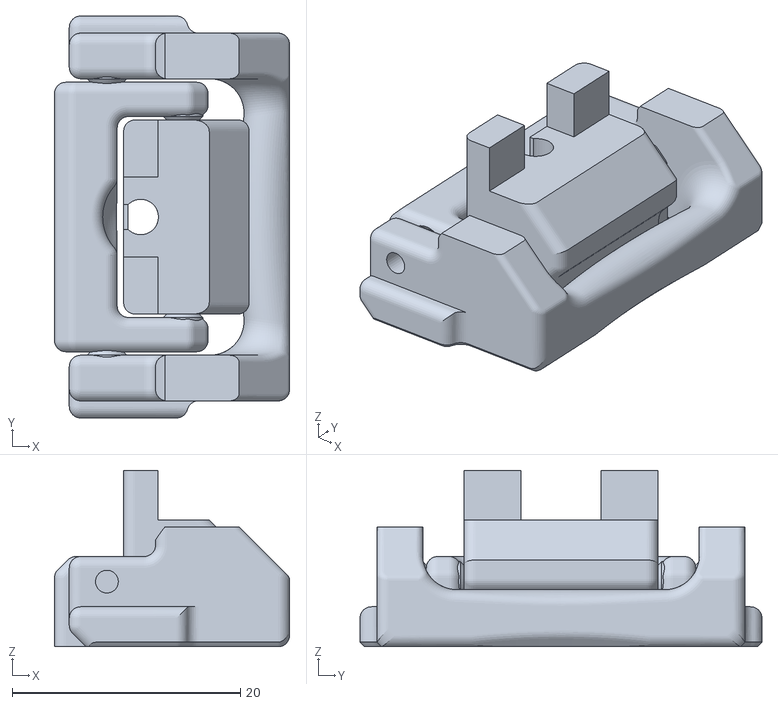
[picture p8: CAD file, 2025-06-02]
mods/PanelAttachement/1515Latch_Remix_Siboor/NewLatch-v0.1-3.0mm-short-legs.stl
20.6 x 35.2 x 15.5

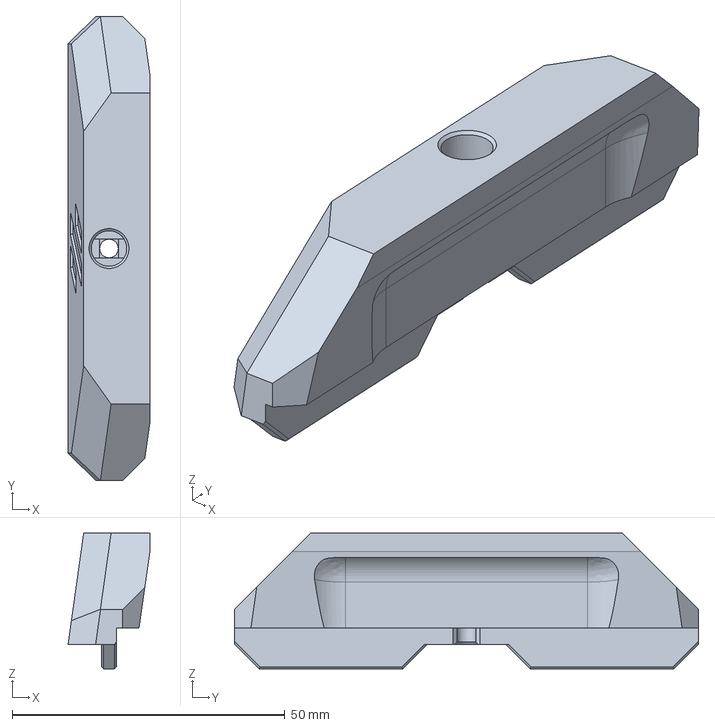
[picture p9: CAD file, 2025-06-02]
mods/PanelAttachement/StealthHandles/CAD/stealth_handle.step
15.0 x 85.0 x 24.9 mm

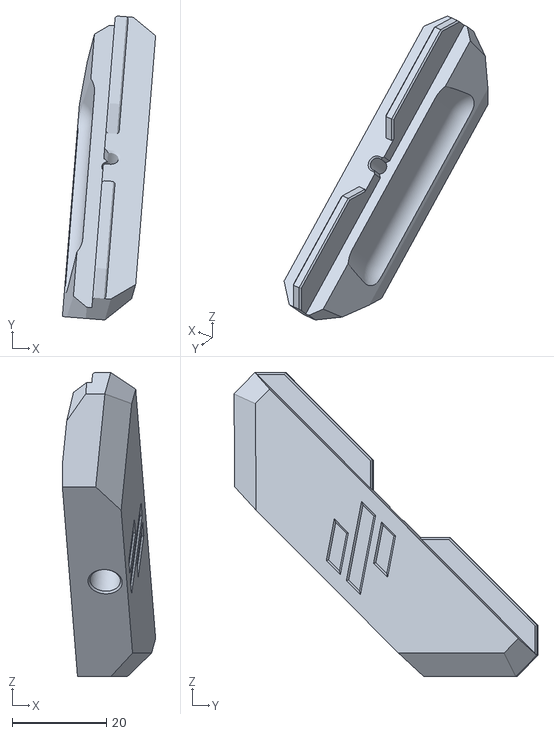
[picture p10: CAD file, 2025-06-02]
mods/PanelAttachement/StealthHandles/STL/handle_b.stl
19.8 x 64.6 x 64.6

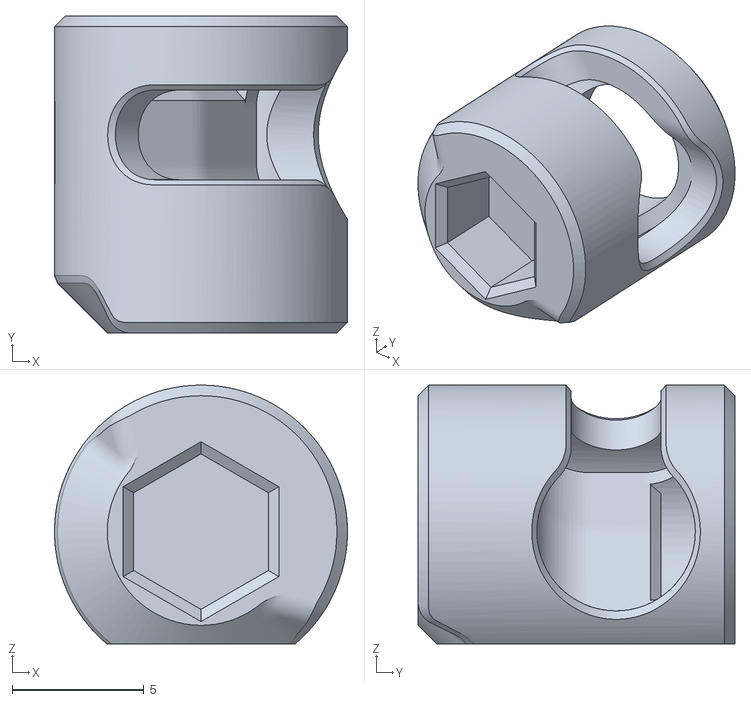
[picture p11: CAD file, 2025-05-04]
mods/R0_Upgrade_R1/[a]_Idler_Cam_Lock_R1_x2.STL
11.1 x 12.0 x 9.80

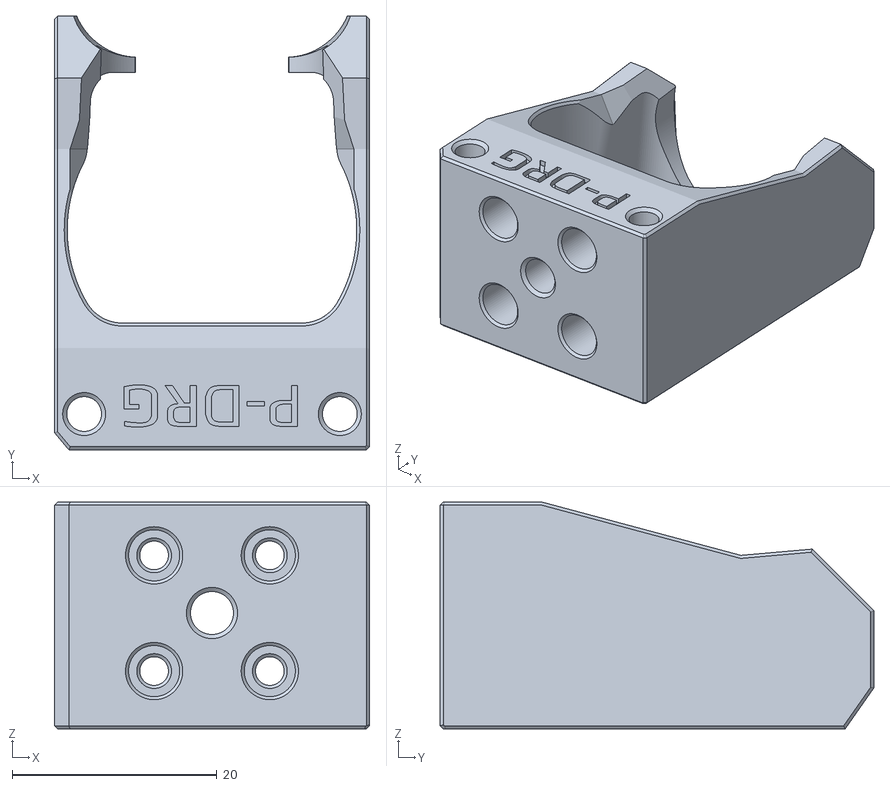
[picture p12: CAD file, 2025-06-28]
mods/Toolhead/MiniStealthBurner/Mounts/DragonHF/FS_Hotend_Mount_Dragon.stl
30.8 x 42.4 x 22.2

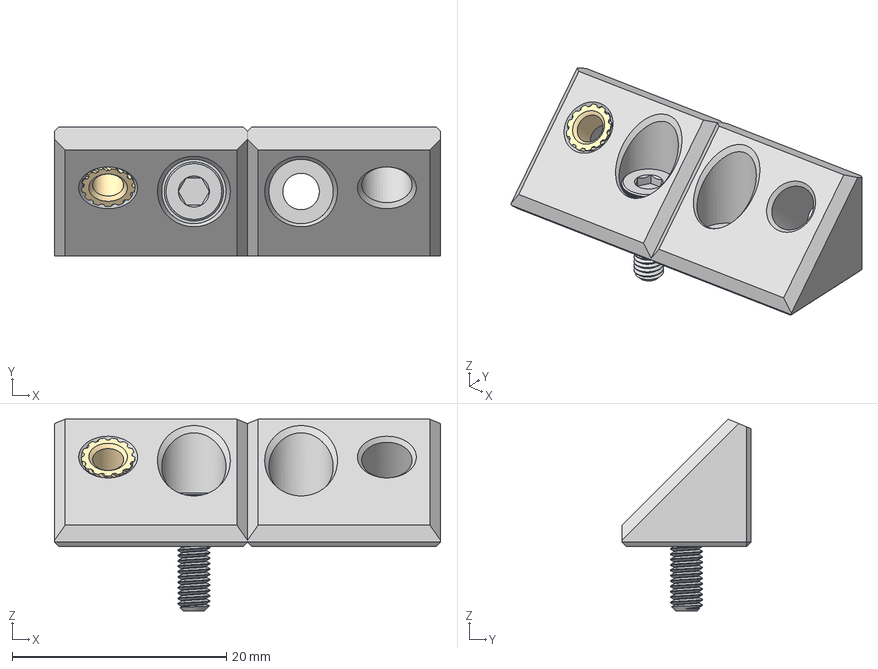
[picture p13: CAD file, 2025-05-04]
mods/DaylightRGBs/Brackets_2020.step
36.0 x 12.0 x 17.9 mm
M3 Threaded Insert
91290A113_Black-Oxide Alloy Steel Socket Head Screw

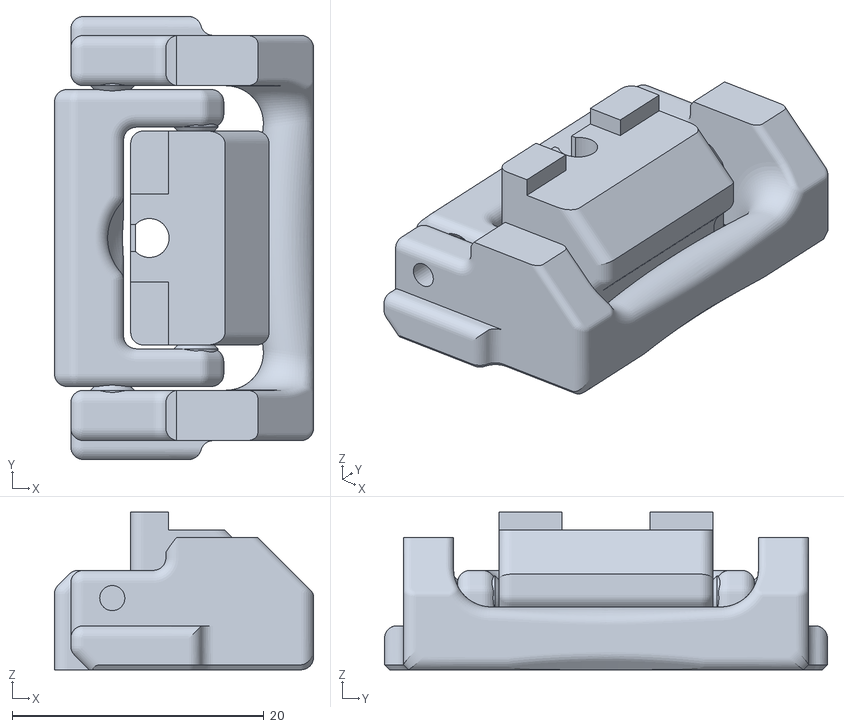
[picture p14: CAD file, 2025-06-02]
mods/PanelAttachement/1515Latch_Remix_Siboor/NewLatch-v0.1-3.0mm-stumps.stl
20.6 x 35.2 x 12.5

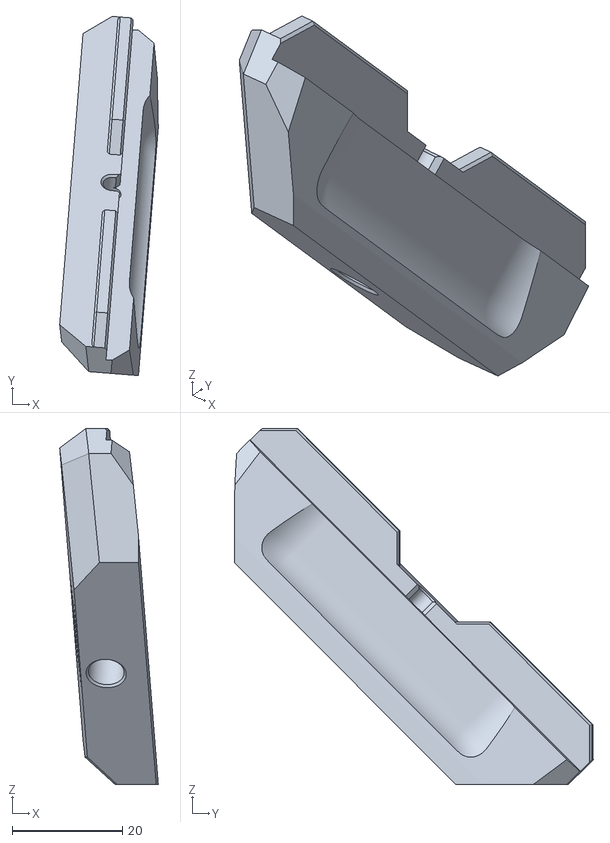
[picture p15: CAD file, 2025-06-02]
mods/PanelAttachement/StealthHandles/STL/handle_a.stl
17.9 x 65.2 x 64.6

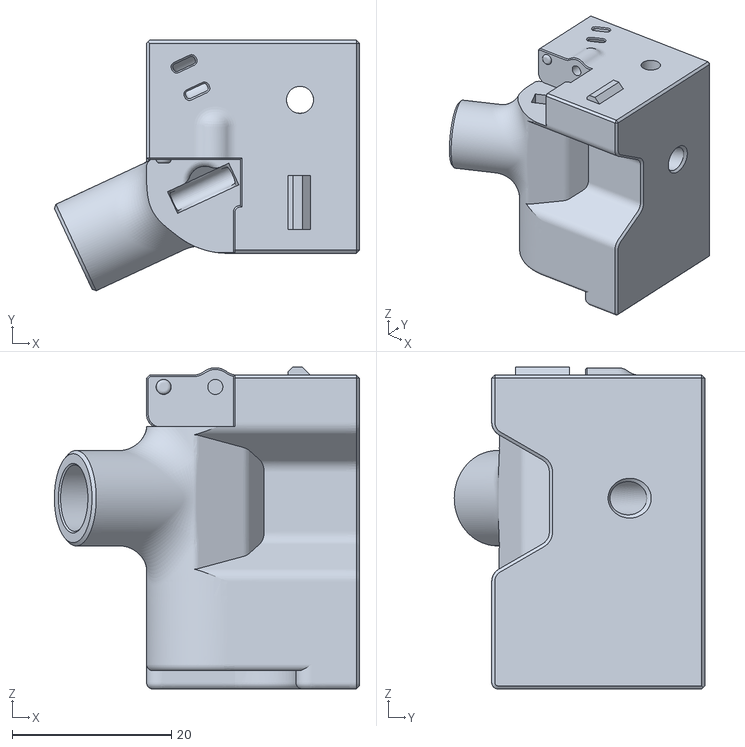
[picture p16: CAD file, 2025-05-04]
mods/R0_Upgrade_R1/Foot_Rear_Right_FRS_R0_x1.STL
38.4 x 31.5 x 40.5

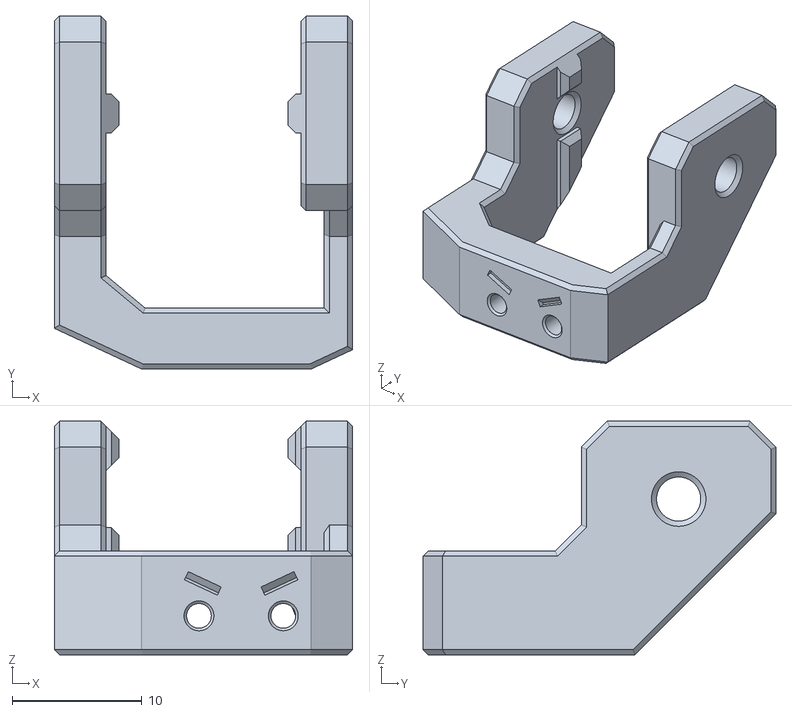
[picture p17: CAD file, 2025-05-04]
mods/R0_Upgrade_R1/[a]_Z_Endstop_Mount_R1_x1.STL
23.0 x 27.2 x 18.0

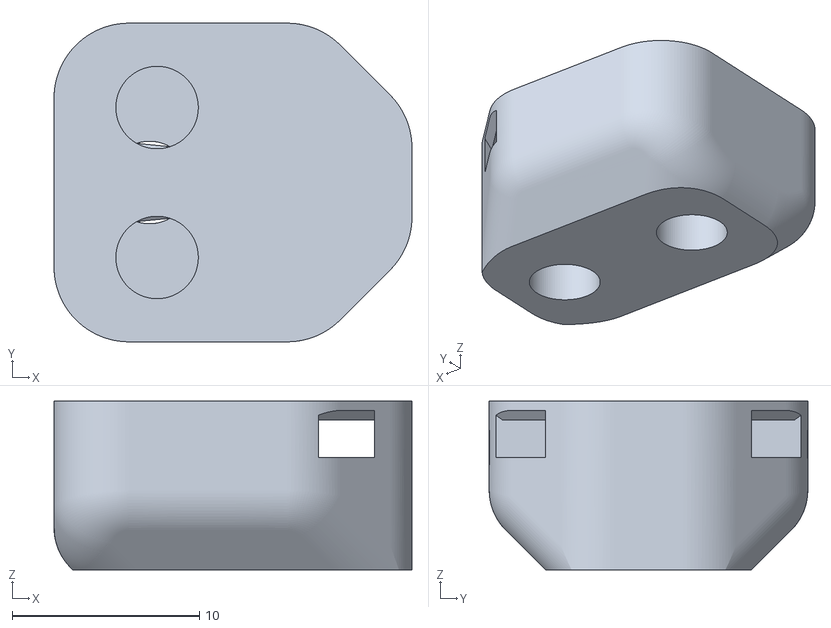
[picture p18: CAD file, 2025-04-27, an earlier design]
mods/KirigamiBed/VORON v0.0_v0.1_legacy_chain_mount.stl
19.1 x 17.0 x 9.00

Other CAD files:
mods/DaylightRGBs/Brackets_1515_x2.step
mods/DaylightRGBs/Brackets_1515_x2.stl
mods/DaylightRGBs/Brackets_2020.stl

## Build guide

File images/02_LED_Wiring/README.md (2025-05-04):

## Setting the LED switch：

### Install the LED Effects Library
This will install the LED Effects for Klipper plugin from [here](https://github.com/julianschill/klipper-led_effect)

SSH into your Fly Gemini

account : ```fly```  
password : ```mellow```  

```shell
cd ~
git clone https://github.com/julianschill/klipper-led_effect.git
cd klipper-led_effect
./install-led_effect.sh
```

### Add to printer.cfg  
```
[output_pin LED]
pin: !PB1
pwm: False
```

## Setting the RGB strip:
### Add to printer.cfg 
```
[neopixel my_neopixel]  
pin:PA9 # Main Board Pin Definitions  
chain_count:24 # Number of RGB's   
color_order: GRB # Colour order  
initial_RED: 0.2 # Red Light on default value is 1 max.  
initial_GREEN: 0.2 # Green Light on default value is 1 max.  
initial_BLUE: 0.2 # Blue Light on default value is 1 max.  
  ```
```
[led_effect rainbow]   
leds:    
    neopixel:my_neopixel  
layers:  
  gradient 0.50 0.50 top (1,0,0),(0,1,0),(0,0,1) 
frame_rate: 24  
  
[led_effect extruder_temp]  
leds:  
    neopixel:my_neopixel  
layers:  
    heater 0.50 0.50 top (0.0,1.0,0.0),(1.0,0.0,0.0),(0.0,0.0,1.0)  
frame_rate: 24  
heater: extruder  
autostart: true  
  
[led_effect bed_heating]  
leds:  
    neopixel:my_neopixel  
layers:  
    heater 0.50 0.50 top (0.0,1.0,0.0),(1.0,0.0,0.0),(0.0,0.0,1.0)  
frame_rate: 24  
heater: heater_bed  
autostart: true  
  ```

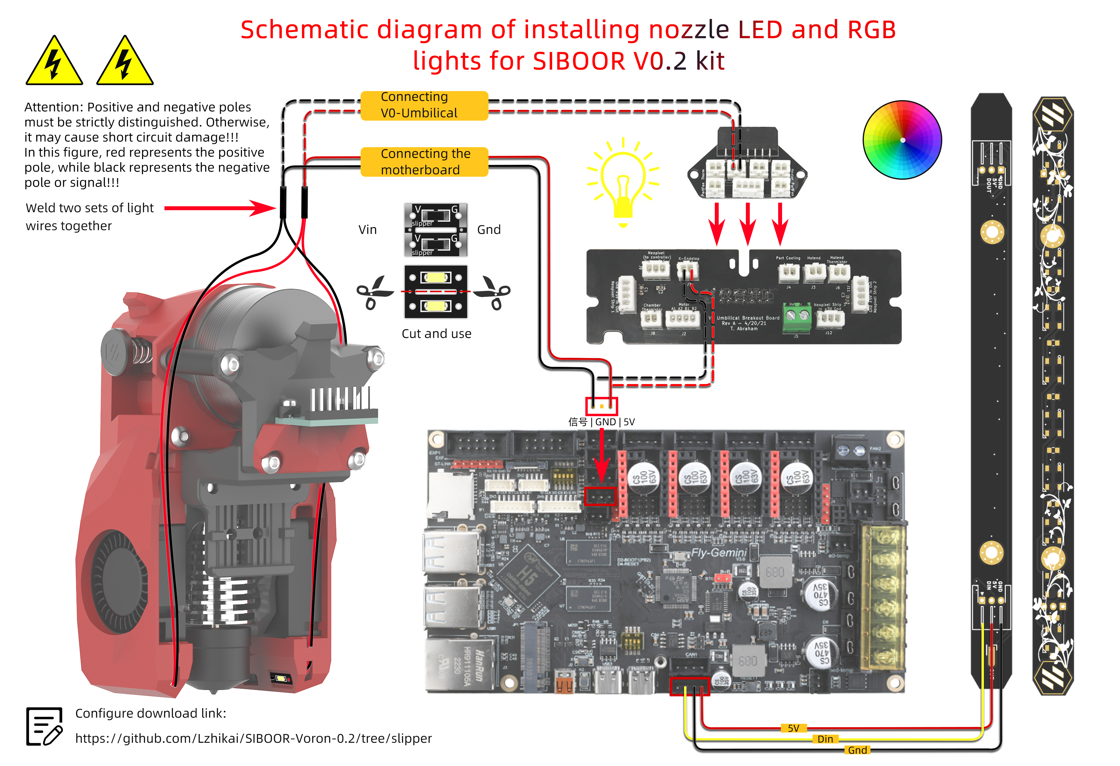
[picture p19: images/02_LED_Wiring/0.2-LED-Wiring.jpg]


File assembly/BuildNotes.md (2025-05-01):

# Mechanical Assembly Build Notes
These are originally notes I took during building.
0 Keiths Notes.txt should be a consise delta to the readme and assembly PDF>

After this the ../future.md

# Overview

These are my assembly notes for: Voron 0.2 R1 (2023 June) by Siboor
  - This had SIBOOR upgrades not part of official Voron, so was called SUBOOR v0.2 R1 (Aug 2023)
  - The kit I had was:
    - Included printed ABS parts (main black, highlights red)
    - Included a Fly Gemini v3.0 mainboard
      - Includes RPI functionality on single board
    - Had the Kirigami bed
    - Upgraded to the Dragon HF Hotend (not TZ-v6-2.0 HoteEnd)
    - Silicon heater 75W (was 60W)
    - Mini Stealthburner with Hot end umbilical toolhead
    - High Temperature Resistant PC Panel
  - TBC RGB indicator

## Specs
- Built Weight: < 7kg
- External Dimensions: 240x240x380 (in mm) 
    - Note: This CANNOT fit in ikea cube even with top-hat removed. The hotend/tubes are too high.
- Printing Size: 120x120x120 (in mm)

## Purchase notes
- I bought from Aliexpress not siboor store (no reason, saw on Aliexpress).
  - I did consider CNC but kept with printed ABS incase wanted to mod later.
    - At time, think some ABS still had to be used ie 1 fut.
  - Went black and red (expect most common); didn't notice option for different extrusions at time of ordering.
    - Kit had note saying: Sunlu red + sublu black
- Was 857.29 plus P&H > 943.02 (at 23-Feb-2023)

## Build Time
- I wasn't rushing and took a while to find deltas from my kit to officail documentation
- Siboor store said 3 days; have seen 30hr estimate.
- I found about a week before powering on doing a few hours most nights and several on weekends.

## References
* [1] README with deltas to official: https://github.com/Lzhikai/SIBOOR-Voron-0.2/blob/main/supplementary/README.md
* [2] Official 0.2: https://github.com/VoronDesign/Voron-0/blob/Voron0.2/Manuals/VORON_V0.2_Assembly_Manual.pdf
* [3] Motors and Feet: https://github.com/Lzhikai/SIBOOR-Voron-0.2/blob/main/supplementary/SIBOOR%20V0.2%20Supplementary%20Manual.pdf
    * For CNC parts (I used ABS)
* [4] Wiring / Motors: https://github.com/Lzhikai/SIBOOR-Voron-0.2/blob/main/supplementary/SIBOOR0.2-supplementary.pdf
* [5] https://github.com/Lzhikai/SIBOOR-Voron-0.2/blob/main/supplementary/SIBOOR%200.2%20R0%20Upgrade%20R1%20Guide.pdf
* [6] Bom: https://github.com/Lzhikai/SIBOOR-Voron-0.2/blob/main/BOM.md
* Root Project from QR Code: https://github.com/Lzhikai/siboor-voron/tree/main/Voron-0.2
* [7] Sourcing guide including Lubricates https://vorondesign.com/sourcing_guide

* Videos:
  * [8] 0.2 Siboor kit build video: https://www.youtube.com/watch?v=zX7Bgzhw0OM&ab_channel=KanduWorkshop
  * [9] 0.2 build video series: https://www.youtube.com/watch?v=-NzwDm4eyQc&ab_channel=Greg%27sMakerCorner
  * [10] 0.2 build series: https://www.youtube.com/watch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
  * [11] 0.1 Bed upgrade (webpage): https://3dpandme.com/2022/03/12/funssor-kirigami-bed-upgrade-for-the-voron-0-1/

# Extras I bought
* Isopropyl alchohol
* WD40 White Lithium Greece (spray can)
    * I used as lubricate for linear rails and screw
* Permatex White Lithium Grease - 80345 for bearings
    * For print head bearings
* Locktight Blue for grub screws
* Super glue for print head nut
    * I had 2 part 5min eproxy
* Cable cutter and stripper
* JST XH connector tool - at least for hotend to Umbiligal PCB
* Optional:
    * Cable management stickies

# Notes:
- Parts:
  - From (1):
    - Extrusion A=B (All tapped)
    - C=H
  - The Kirigami bed deprecates:
    - 100mm "F Extrusion" x2 (end M3)
    - 100mm "G Extrusion" x1 (27.5x2 same face)
    - ~ page 38 (note says to skip to page 43)
  - There are separate extrusions in the kit for the lid
- I think these were omitted below so including here to ensure captured
  - Alignment tools ~ 19min of https://www.youtube.com/watch?v=zX7Bgzhw0OM&list=WL&index=6&ab_channel=KanduWorkshop
  - Motor B/X is top left  when viewed from the front
  - Motor A/Y is top right when viewed from the front
  - I didn't sand axel so gears more free (~p160)
  - Something about [4] p9
    - I didn't do this, at least not initially. It also required splicing both in parallel
- Clarification
  - p21 
    - These were leavered arms in first tray
  - p36 'Frame - Component Prep' this is all bed tray
    - MOD: Have Kirigami which mentions skip (on p38) but is here
      - These two parts are part of metal tray for Kirigami.
      - A Kirigami v0 install video is at: https://www.youtube.com/watch?v=eOnNvhircn8&ab_channel=MapleLeafMakers
        - I have v0.2 which has some mods coming up:
      - The part on p36 is deprecated:
        - It WAS 'VORON v0.0_v0.1_legacy_chain_mount.stl
'https://github.com/christophmuellerorg/voron_0_kirigami_bed/blob/master/STL/VORON%20v0.0_v0.1_legacy_chain_mount.stl with install guidance on at 7:27
        - I had BLACK 'Voron_0.2_stealth_chain_mount.stl'  https://github.com/christophmuellerorg/voron_0_kirigami_bed
        - This is installed like: https://github.com/christophmuellerorg/voron_0_kirigami_bed/blob/master/Images/stealth_beta.png
        - NB: My dragchain ends were same, the v0.1 mentions one goes BOTH ways and use that on tray
      - There is another BLACK part which is shown in red with a Z on https://github.com/christophmuellerorg/voron_0_kirigami_bed/blob/master/Images/stealth_beta.png
        - This needed 1x M3 heat insert and 4x M3x6 BHCS
      - Keep the lead screw with anti-back lash mount attached until mouting z-axis motor.
          - The part shown in RED with the Z was BLACK in my kit
          - Mount with the horizontal part at top (I originally did bottom and notied at p92 - leasily swapped)
        - Electronics used 3x6
      - Returns to manual after attached p47 (covered by https://github.com/christophmuellerorg/voron_0_kirigami_bed/blob/master/Images/stealth_beta.png)

  - p49-51; have an update to z endmount stops in 0.2 R1 upgrade
      - this is shown in (5) as z endstop mount; the red one with frowny eye-brows
      - uses 2x M2x10 self tapping from switch outside. Red switch on RHS from front
      - then tried M3x8 BHCS into frame
    - https://www.youtube.com/watch?v=zX7Bgzhw0OM&list=WL&index=4&ab_channel=KanduWorkshop @3:37 shows a red part;

  - p53; I added extra 2 nuts to allow for 5VPSU mounting in fuure if required (kit has all in 1 board)

  - p70; shims M3x6x0.5
    Spacer is red ~10mm

  - 81 used lock-tight on grub screws

  - 92 for Kirigami skip this; will mount with lead screws from motor to tray in p104
    - From TODO the mount should be attached to tray as in https://github.com/christophmuellerorg/voron_0_kirigami_bed/blob/master/Images/stl_mounting.png 
    - Kept the lead screw attachment connected to the lead screw but if unattached wait until p104 (as will lubricate)
      - This is consistent with:
        - 0.1 tray upgrade: https://3dpandme.com/2022/03/12/funssor-kirigami-bed-upgrade-for-the-voron-0-1/
        - https://www.youtube.com/watch?v=zX7Bgzhw0OM&list=WL&index=4&ab_channel=KanduWorkshop at 4:21

  - p73 + p79; don't over tighten these bolds into the motor at this stage
    - The belt tensioner will shift them later (p135).

  - p95 NB 4xM3 nuts on back right virtical, confirm at p97
  - p105 for Kirigami bed, this also needed screw nut attached to bed
    - For threaded rod lubrication I used white lithium greace, same as linear rails (WD40)
       - If need to reattach have tallest part facing up:
            - See https://www.youtube.com/shorts/Y4ScC2dLlLY (linked from manual p92)
      - To attach screw nut to Kirigami bed I used M3x12 (to match p92)

  - p113 suggest not tightening nuts to attach linear rail so it is centerd (p118)

  - p121; I added another 3 nuts to each side to mount carry handles as a future mode
    - eg: https://www.printables.com/model/550363-voron-02-carrying-handles/files
    - I probably would have preferred it on lower handle but thought about it too late.

  - p129; the kit allowed 102x3 lengths so I cut 3 to same length to have a spare.
      - I fed each part through the x-carriage slot temporarily to 'zipper' together to check teath same
      - Potentially off-by-one but will tune to 110Hz to ensure ok (p135)

  - p130
    - My belt tensions didn't move, which traced to shims bining into ABS when attached motors in on p73 + p79
      - Luckily I had some larger M3 washers that fit in the slot without being bound so could be attached.
    - Have suggestion to temporarily mount x-carriage to linear rail with M2x6 (p134) while threading belt
      - See https://www.youtube.com/watch?v=_PidL01HJL8

  - p131 count teath is useful but will be trimming belts flush later (p136) to allow toolhead to be attached

  - p134; I droped the thread lock into a hole and pushed with end of pliers (filament was too thick), ensure wipe off before attaching ABS x-carriage.

  - p135 I used 'pano tuner'; hard to set exact; got 123 with logic will quickly loosen.

  - p145 I WANTED to use the left over silcon spaces I had rather than yellow spings
    - However extended beyond printer and front over heat pad so would need to cut down to fit. Potential in future but for now keep yellow spings
    - The M3x40 screws are very long but confirmed do not hit when bed is at the bottom

  - p146; will wire kirigami bed header later. For now tuck out of the way under the heater pad

  - p147 for Kirigami v2 bed dragchain was already assembed so can skip

  - p151 can skip the 'standoff' heatset inserts. There is an aluminium replacement part now
    - This is installed at p180 (on bsvk of screws holding extruder motor)

  - p153 didn't notce a built in support

  - p154 bottom bearing may have already mounted, possibly friction fit.
    - I could remove by placing in p155 part, or some needle nose pliers.
    - The design should allow these to be easily align for gear to vertically align with gear gripping the filament.
      - Mine was originally too tight (could fit with force), even with some sanding.
        - Further sanding was required to assist in self aligning.
        - The other gear and grub thread needs to go past this later (p158)
        - Add axel into drill to help sanding maybe 10sec using 80 grit paper I had.
          - eg 58:24 https://www.youtube.com/watch?v=3Z6UbegCPGA&list=PLiiEyXLrqIBSOPptPnDcVc-NQQFDGW8lQ
          - cleaned after with some isopropyl alchol
    - Not no 3d printed space but was already correct length
      - Apparently if too long can mount and bind later in usage.

  - p155 I used 2part eproxy resin (5min) to glue nut; then held down with temp screw
    - avoid thread locker as can sometimes impact ABS

  - p157 I tried but stopped, in hindsight it would have worked:
    - Added 1-2xM3 shims to Hinge Pin to assist it but need to ensure hight doesn't impact clearance during p160
    - These were spare from washers added to tensioning arm previously

  - p158 if the gear had trouble fitting onto shaft further sand.
    - Ideally bearings allow axel to freely move up and down, and gear can move within cutout section.
    - I did NOT lock tight this grub screw as only loosly fitted atm. It is in the flat section of shaft

  - p160 I found best to add shims to top and bottom to keep axel spaced, then when gear added can remove. The gear and filament is what self senters.

  - p165 had 2 sets of fans; blower fans both 3010 24V 0.1A
    - blower fans as those without exposed fan
    - they needed a plastic clip removed, but note array first (I transfered with silver marker)
      - See 6:30 of https://www.youtube.com/watch?v=zX7Bgzhw0OM&list=WL&index=4&ab_channel=KanduWorkshop at 4:21
    - Add the hotend fan (p166) - used shorter cable DC24V 0.1A BEFORE right fan (viewed from rear) routing through same channel

  - p169 I removed the tension knob from 162 to get better access but can be worked around
    - This is needed in next step anyway

  - p174 I had a phaetus dragon which mounted with M3x8  SHCS
    - I used some blue capricorn tubing for PTFE (is lower diameter) mainly for looks.
    - There is the jig on p176, I found ~20mm to be the final and was easily to trim a slight excees

  - p177 I gound backet writing had to be to BACK (motor side)
    - The hootend tapered side is to back, and has more poking out at back.
      - See 7:32 of https://www.youtube.com/watch?v=zX7Bgzhw0OM&list=WL&index=4&ab_channel=KanduWorkshop
    - NOT discussed; hotend cartrige and thermister. as at 8:08front fan. Added these before mouting.

  - p180 looks different, more like a man with several cutouts; bottom half same
    - Used all M3x8 (no M3x6); also attached umbilical PCB
    - Added zip ties to arms and routed similar to p182

  - p185
    - See (4) to mount standoffs for mobo before inserting panel.
      - Think (4) panel is upside down to (1)
      - p186 swapped insert so heatsinks on top right
        - Followed 9:50 of https://www.youtube.com/watch?v=zX7Bgzhw0OM&list=WL&index=5&ab_channel=KanduWorkshop
          - I had a long fan cable so no issues of what is mentioned.
    - Notes:
      - Mobo does cover some mounting screws, so removed to swap
      - Remove film before inserting panels
      - 2x Extra screws per panell cannot be accessed so were unnecessary
        - two on side away from ethernet can be added to plastic
    - > Skip to 191

  - p192; added M3x6 screws as well as tape

  - p193 this part needs the 4x heatsets shown on p187

  - p200 > [4] p4-7
    - I wired up Kirigami bed
      - Cable management I added a heatset and M3x12 to attach
    - No light to front of bed yet
      - Believe on wiring diagram but wait until later. Unsure of dragchain spaec too
    - > Returns 205

  - p218 + 219 > Replaced with umbilical PCB and red cable pass through bracket

  - Notes on case parts - have a tab goes along top/bottom to align parts

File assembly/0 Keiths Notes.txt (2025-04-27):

Keiths notes for: Voron 0.2 R1 (2023 June) by Siboor

References:
  1. README with deltas to official: https://github.com/Lzhikai/SIBOOR-Voron-0.2/blob/main/supplementary/README.md
  2. Official 0.2: https://github.com/VoronDesign/Voron-0/blob/Voron0.2/Manuals/VORON_V0.2_Assembly_Manual.pdf
  3. Motors and Feet: https://github.com/Lzhikai/SIBOOR-Voron-0.2/blob/main/supplementary/SIBOOR%20V0.2%20Supplementary%20Manual.pdf
  4. Wiring / Motors: https://github.com/Lzhikai/SIBOOR-Voron-0.2/blob/main/supplementary/SIBOOR0.2-supplementary.pdf
  5. https://github.com/Lzhikai/SIBOOR-Voron-0.2/blob/main/supplementary/SIBOOR%200.2%20R0%20Upgrade%20R1%20Guide.pdf
  6. Bom: https://github.com/Lzhikai/SIBOOR-Voron-0.2/blob/main/BOM.md
Root Project from QR Code: https://github.com/Lzhikai/siboor-voron/tree/main/Voron-0.2

Extras:
  - WD40 White Lithium Greece (spray can)
    - I used as lubricate for linear rails and screw
  - Locktight Blue for grub screws

Purchase notes:

I bought from Aliexpress and didn't see extrusion options. I did consider CNC but went away as at least 1 foot had to be plastic and original designs were ABS incase wanted to mod later.
  - Went black and red (expect most common).
    - Kit had note saying: Sunlu red + sublu black

---
Parts:
  - From (1):
    Extrusion A=B (All tapped)
    C=H
  - The Kirigami bed deprecates:
      - 100mm "F Extrusion" x2 (end M3)
      - 100mm "G Extrusion" x1 (27.5x2 same face)
      ~ page 38 (note says to skip to page 43)
  - There are separate extrusions in the kit for the lid

  - p21 
      > These were leavered arms in first tray
  - p36 'Frame - Component Prep' this is all bed tray
    > MOD: Have Kirigami which mentions skip (on p38) but is here
      - These two parts are part of metal tray for Kirigami.
      - A Kirigami v0 install video is at: https://www.youtube.com/watch?v=eOnNvhircn8&ab_channel=MapleLeafMakers
        - I have v0.2 which has some mods coming up:
      - The part on p36 is deprecated:
        - It WAS 'VORON v0.0_v0.1_legacy_chain_mount.stl
'https://github.com/christophmuellerorg/voron_0_kirigami_bed/blob/master/STL/VORON%20v0.0_v0.1_legacy_chain_mount.stl with install guidance on at 7:27
        - I had BLACK 'Voron_0.2_stealth_chain_mount.stl'  https://github.com/christophmuellerorg/voron_0_kirigami_bed
        - This is installed like: https://github.com/christophmuellerorg/voron_0_kirigami_bed/blob/master/Images/stealth_beta.png
        - NB: My dragchain ends were same, the v0.1 mentions one goes BOTH ways and use that on tray
      - There is another BLACK part which is shown in red on https://github.com/christophmuellerorg/voron_0_kirigami_bed/blob/master/Images/stealth_beta.png
        - This needed 1x M3 heat insert and 4x M3x6 BHCS
      - Keep the lead screw with anti-back lash mount attached until mouting z-axis motor.
          - The part shown in RED with the Z was BLACK in my kit
          - Mount with the horizontal part at top (I originally did bottom and notied at p92 - leasily swapped)
        - Electronics used 3x6
      >> Returns to manual after attached p47 (covered by https://github.com/christophmuellerorg/voron_0_kirigami_bed/blob/master/Images/stealth_beta.png)

  - p49-51; have an update to z endmount stops in 0.2 R1 upgrade
      - this is shown in (5) as z endstop mount; the red one with frowny eye-brows
      - uses 2x M2x10 self tapping from switch outside. Red switch on RHS from front
      - then tried M3x8 BHCS into frame
    - https://www.youtube.com/watch?v=zX7Bgzhw0OM&list=WL&index=4&ab_channel=KanduWorkshop @3:37 shows a red part;

  - p53; I added extra 2 nuts to allow for 5VPSU mounting in fuure if required (kit has all in 1 board)

  - p70; shims M3x6x0.5
    Spacer is red ~10mm

  - 81 used lock-tight on grub screws

  - 92 for Kirigami skip this; will mount with lead screws from motor to tray in p104
    - From TODO the mount should be attached to tray as in https://github.com/christophmuellerorg/voron_0_kirigami_bed/blob/master/Images/stl_mounting.png 
    - Kept the lead screw attachment connected to the lead screw but if unattached wait until p104 (as will lubricate)
      - This is consistent with:
        - 0.1 tray upgrade: https://3dpandme.com/2022/03/12/funssor-kirigami-bed-upgrade-for-the-voron-0-1/
        - https://www.youtube.com/watch?v=zX7Bgzhw0OM&list=WL&index=4&ab_channel=KanduWorkshop at 4:21

  - p95 NB 4xM3 nuts on back right virtical, confirm at p97
  - p103 foot accents were in red

-----

 >>> 104
  - You will need to remove lead screw to mount red plate
    - I used white lithium greece; same as linear rails

       - If need to reattach have tallest part facing up:
            - See https://www.youtube.com/shorts/Y4ScC2dLlLY (linked from manual p92)

  Add nutes to allow for carry handles on next extrusions

  Next deltas; 126,154

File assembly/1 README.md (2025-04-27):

# This guide covers the differences between the SIBOOR 0.2kit and the original VORON0.2 tutorial, and includes instructions on wiring and debugging.
# The supplement also contains the differences section of Siboor V0.2. updated 2023/7/4
# You can download and view the official PDF assembly tutorial of VORON here：[Voron-0.2/Manuals](https://github.com/VoronDesign/Voron-0/tree/Voron0.2/Manuals)  · GitHub
***Github SIBOOR V0.1 kit assembly manual instruction.***

* Page 13-15  ：In SIBOOR V0.2 kit, EXTRUSION A and EXTRUSION B are combined into one EXTRUSION, both of which have been tapped and are common to each other. C EXTRUSION and H EXTRUSION are combined into one EXTRUSION, both of which are drilled and tapped, which are common to each other.

* Page 18 ：The SIBOOR V0.2 kit uses the guide strip of purple PCB, so it does not need to use the printed parts and embedded M2 nut.

* Page 23 ：SIBOOR V0.2 kit is not equipped with NO DROP NUTS

* Page 20、24 和 113  ：As described above, two purple PCBs are used as guide rail fixing strips to fix the MGN7 guide rail.

* Page 48  ： The SIBOOR V0.2 kit is already equipped with a soldered Endstop, plug and play.

* Page 142 ：For SIBOOR V0.2 kit, the heating bed has already lifted the prefabricated fuse. please skip this step

* Page 154 ：Make sure that the bearing is flush with the shaft, otherwise it will cause friction between the metal shaft and the motor. Place the side of the bearing flat on the table and press the white gear with both thumbs to make the bearing flush with the shaft.

* Page 173 ：Use 4 pieces of M2.5×8 screws to fix the CHC V6 hot end

* Page 184  ：SIBOOR V0.2 kit, using a two in one Gemini motherboard, using four nylon posts and M3 × 8 Screws are fixed on the acrylic panel.

* Page 192 ：In addition to using double-sided adhesive tape to fix the power supply, you can also choose to install two M3 × 6 screws on the reverse side to fix the power supply.

* Page 199- 205 ：See the SIBOOR V0.2 kit supplementary instructions separatel

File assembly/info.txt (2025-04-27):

To access printer found best in chrome: http://192.168.7.60/#/

TODO:
	1. Continue with PDF (p21/30)
		- Extruder tuning
		- Setup Cura including Octoprint

	2. Continue with: https://jjarrard.github.io/Gemini-V3-Flash-Voron-V0/installation/
		- Anything on z-offset
		- Anything on z-homing
		- Anything on Z stop at bottom but home to top??

	3. Redo PIF Tuning
	4. Initial test print

	- Accelerometer - input shaping

	- Backup my config files -> My GIT
	- Cleanup notes and host somewhere -> my git

STRETCH:

	- Image SD card then try updating

	- Try copying configs of other SD card

	- Check BED LED - old FW used it
		https://docs.siboor.com/other-products/led-effect-notes/installing-led-effects-software

FUTURE:
	- See if any recommended USB cameras
		- Missing one of my logitect; did try 2 other

=======

Info:
	- Screen speed: 115200
	- IP: 192.168.7.60
		I believe it only supports 2.4GHz WiFi
			/etc/NetworkManager/system-connections/Keithino.nmconnection 
	- Default password was: mellow -> speedy
		https://docs.siboor.com/siboor-0.2-r1-aug/the-build/initial-startup
		User: fly
	- PID Tuning: $ PID_CALIBRATE HEATER=heater_bed TARGET=85
		// PID parameters: pid_Kp=64.897 pid_Ki=3.576 pid_Kd=294.468
	- PID_CALIBRATE HEATER=extruder TARGET=210
		// PID parameters: pid_Kp=29.663 pid_Ki=1.676 pid_Kd=131.259

	- FANS care about +/- escpecially hotend fan

Follow: https://docs.siboor.com/siboor-0.2-r1-aug/the-build/initial-startup

====
	Input shaper
		Canuck creator had a crash course --> Aborted will find a Gemini based on

		Install:
			~/klippy-env/bin/pip install -v numpy # -> Already existed
			sudo apt install python3-numpy python3-matplotlib # -> Already existed. NB video omitted python3

		STOPPPED when wanted to download and update klipper
====

Image:
	System Image:
		- https://mellow.klipper.cn/en/docs/ResDownload/system-img/fly-Gemini/?persistLocale=true
			default user: fly
			password: mellow

		- Do NOT update
			Due to server issues, please do not update the system or klipper arbitrarily
			Please download FLY OS system, installing the original Armbian is too difficult and not recommended

		- Follow from: https://mellow.klipper.cn/en/docs/ResDownload/system-img/fly-Gemini
			cd klipper
			make clean
			make menuconfig
				> setup to match

		- FYI Serial: /dev/serial/by-id/usb-Klipper_stm32f405xx_28003D001547323330373434-if00
			> Config file at: /home/fly/printer_data/config/printer.cfg

On MBP
	- Connecting USB cable did power on board 
		- Don't power through USB hub - used dock
		- This was USB C closer to ethernet port 'USB3'
	- Detect Port:
		ls /dev/*usb*
		/dev/cu.usbserial-230	/dev/tty.usbserial-230
		Note:
			- From: https://pbxbook.com/other/mac-tty.html#screen
			  Suggest using cu:
				TTY devices are for calling into UNIX systems.
				CU (Call-Up) devices are for calling out from them (eg, modems).
				We want to call-out from our Mac, so /dev/cu.* is the correct device to use.

				The technical difference is that /dev/tty.* devices will wait (or listen) for DCD (data-carrier-detect), eg, someone calling in, before responding. /dev/cu.* devices do not assert DCD, so they will always connect (respond or succeed) immediately.
			- However ChatCPT screen example uses tty

		https://github.com/Jjarrard/Gemini-V3-Flash-Voron-V0/tree/main/Config%20Files

	- Used screen connecting to cu port at 115200
		screen /dev/cu.usbserial-230 115200

		This will drop into a console shell: root@flygemin
		To exit: Ctrl+A + Ctrl + \

		- I did a reboot and noticed
			[FAILED] Failed to start Resets System Activity Logs.
				See 'systemctl status sysstat.service' for details.

		- From manual: nmtui
			Active a connection
				WiFi:	I could only see the 2.4 GHz option
					keithino
				Suggest using Ethernet if need higher speed, especially in the study
			Set Hostname:
				voron0201
		- Reserved:
			MAC: 1C-78-39-0B-34-EF
			Keithino: 192.168.7.60
				(Unreserved was: 192.168.7.124)

		- Initially Confirmed can access fluid in web browser: 192.168.7.60
			mcu 'display': Unable to connect
			Once the underlying issue is corrected, use the
			"FIRMWARE_RESTART" command to reset the firmware, reload the
			config, and restart the host software.
			Error configuring printer

			At this stage the Voron was powered over USBC

		- Attempt to update
			apt update
			apt upgrade
			> This Broke Klipper / mainsail. Will return to this

	- Front Display
		- FYI There is a similar HW (LDO Motors v0.1) at: https://www.youtube.com/watch?v=a66HdK4VCd8
			- Confirmed the wiring is red-white-green-black; this video swaps data pins swapped ~10min
		- With multimeter I confirmed my cable was pinned correctly
		- Need 3.3v boot jumper to enter boot mode
		- Confirmed lsusb shows up device (diff b4 and after connected):
			- Bus 007 Device 002: ID 0483:df11 STMicroelectronics STM Device in DFU Mode
		- From: https://docs.siboor.com/siboor-0.2-r1-aug/the-build/initial-startup
			cd ~/klipper/
			make -j4 flash FLASH_DEVICE=0483:df11

			< This had failed to validate messages. Was pushing 23204 bytes >
			Note:
				1. https://community.particle.io/t/solved-dfu-util-error-during-download-get-status-error-writing-firmware/13329

				dfu-util has known issue where it both reports success and failure. (See lines mentioning done and success, and the last line mentioning error.) You can ignore this error, the tool is lying to yo

			Similar with:
				make flash FLASH_DEVICE=0483:df11
				Also with Sudo
			sudo reboot
			< I then removed jumper and pressed display reset PB and it all worked :) >

STRETCH:
	- Look at any dmesg warnigs
		 dmesg --level=err,warn
	- Suggest do NOT do apt updates on this image: https://www.reddit.com/r/VORONDesign/comments/1evy21o/how_do_i_get_a_fly_gemini_v3_working/
		> BBT Octopus and a Pi5
		- Did have issues getting passed uboot when did
			sudo apt-get --with-new-pkgs upgrade <pkg>
				For: linux-dtb-current-sunxi64 linux-image-current-sunxi64
				Trying to avoid The following packages have been kept back:

# Future:
	- Mods others have done
		https://www.wirewd.com/make/voron0v2

Notes:
	- dfu-util error attempting to flash front display
			https://docs.siboor.com/siboor-0.2-r1-aug/the-build/initial-startup
			cd ~/klipper/
			make -j4 flash FLASH_DEVICE=0483:df11
		The make command did have a sudo prompt but even then seem to not be able to validate
		This was with jumper connected.
			$ make -j4 flash FLASH_DEVICE=0483:df11
			  Creating symbolic link out/board
			  Building out/autoconf.h
			  Compiling out/src/sched.o
			  ...
			  Preprocessing out/src/generic/armcm_link.ld
			  Building out/compile_time_request.o
			Version: v0.10.0-391-g722ad4a1-dirty-20250329_224958-voron0201
			  Linking out/klipper.elf
			  Creating hex file out/klipper.bin
			  Flashing out/klipper.bin to 0483:df11
			sudo dfu-util -d ,0483:df11 -R -a 0 -s 0x8000000:leave -D out/klipper.bin

			[sudo] password for fly: 
			dfu-util 0.9

			Copyright 2005-2009 Weston Schmidt, Harald Welte and OpenMoko Inc.
			Copyright 2010-2016 Tormod Volden and Stefan Schmidt
			This program is Free Software and has ABSOLUTELY NO WARRANTY
			Please report bugs to http://sourceforge.net/p/dfu-util/tickets/

			dfu-util: Invalid DFU suffix signature
			dfu-util: A valid DFU suffix will be required in a future dfu-util release!!!
			Opening DFU capable USB device...
			ID 0483:df11
			Run-time device DFU version 011a
			Claiming USB DFU Interface...
			Setting Alternate Setting #0 ...
			Determining device status: state = dfuERROR, status = 10
			dfuERROR, clearing status
			Determining device status: state = dfuIDLE, status = 0
			dfuIDLE, continuing
			DFU mode device DFU version 011a
			Device returned transfer size 2048
			DfuSe interface name: "Internal Flash  "
			Downloading to address = 0x08000000, size = 23204
			Download	[=========================] 100%        23204 bytes
			Download done.
			File downloaded successfully
			dfu-util: Error during download get_status

			Failed to flash to 0483:df11: Error running dfu-util

			If the device is already in bootloader mode it can be flashed with the
			following command:
			  make flash FLASH_DEVICE=0483:df11
			  OR
			  make flash FLASH_DEVICE=1209:beba

			If attempting to flash via 3.3V serial, then use:
			  make serialflash FLASH_DEVICE=0483:df11

			make: *** [src/stm32/Makefile:82: flash] Error 255
		  make serialflash FLASH_DEVICE=0483:df11

		make: *** [src/stm32/Makefile:82: flash] Error 255

	- Boot Messages:
		- Had note: "sudo apt update && sudo apt install armbian-config"
			Running thishad: W: GPG error: https://github.armbian.com/configng stable InRelease: The following signatures couldn't be verified because the public key is not available: NO_PUBKEY 93D6889F9F0E78D5

			E: The repository 'https://github.armbian.com/configng stable InRelease' is not signed.

		- From https://forum.armbian.com/topic/23465-apt-get-update-fails-with-public-key-errors/page/2/#comment-172106
			sudo wget https://apt.armbian.com/armbian.key -O key
			sudo gpg --dearmor < key | sudo tee /usr/share/keyrings/armbian.gpg > /dev/null
			sudo chmod go+r /usr/share/keyrings/armbian.gpg
			sudo echo "deb [arch=$(dpkg --print-architecture) signed-by=/usr/share/keyrings/armbian.gpg] http://apt.armbian.com $(lsb_release -cs) main  $(lsb_release -cs)-utils  $(lsb_release -cs)-desktop" | sudo tee /etc/apt/sources.list.d/armbian.list
			sudo apt update

Resources:
	Unsure if have flagged above

		- Initial setup:
			- https://docs.siboor.com/siboor-0.2-r1-aug/the-build/initial-startup
			- https://docs.vorondesign.com/build/startup/

		- Images and configs:
			- https://mellow.klipper.cn/en/docs/ResDownload/system-img/fly-Gemini/?persistLocale=true
			- https://jjarrard.github.io/Gemini-V3-Flash-Voron-V0/installation/
			- Gemini Board CFG: https://mellow-3d.github.io/fly-gemini_v3_klipper_mcu_config.html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
			- Debugging: https://docs.vorondesign.com/community/troubleshooting/eddie/klipper_common_errors.html

		- Kirigami Bed: https://docs.siboor.com/other-products/v0-krigami-bed
			- https://docs.siboor.com/other-products/led-effect-notes/installing-led-effects-software

		- Misc Voron:
			- https://docs.vorondesign.com/build/software/
			- https://github.com/VoronDesign/Voron-0/tree/Voron0.2r1/Firmware

		- Potential upgrades:
			- https://github.com/Lzhikai/SIBOOR-Voron-0.2/blob/main/expander/README.md
			- https://github.com/Lzhikai/SIBOOR-Voron-0.2/tree/main

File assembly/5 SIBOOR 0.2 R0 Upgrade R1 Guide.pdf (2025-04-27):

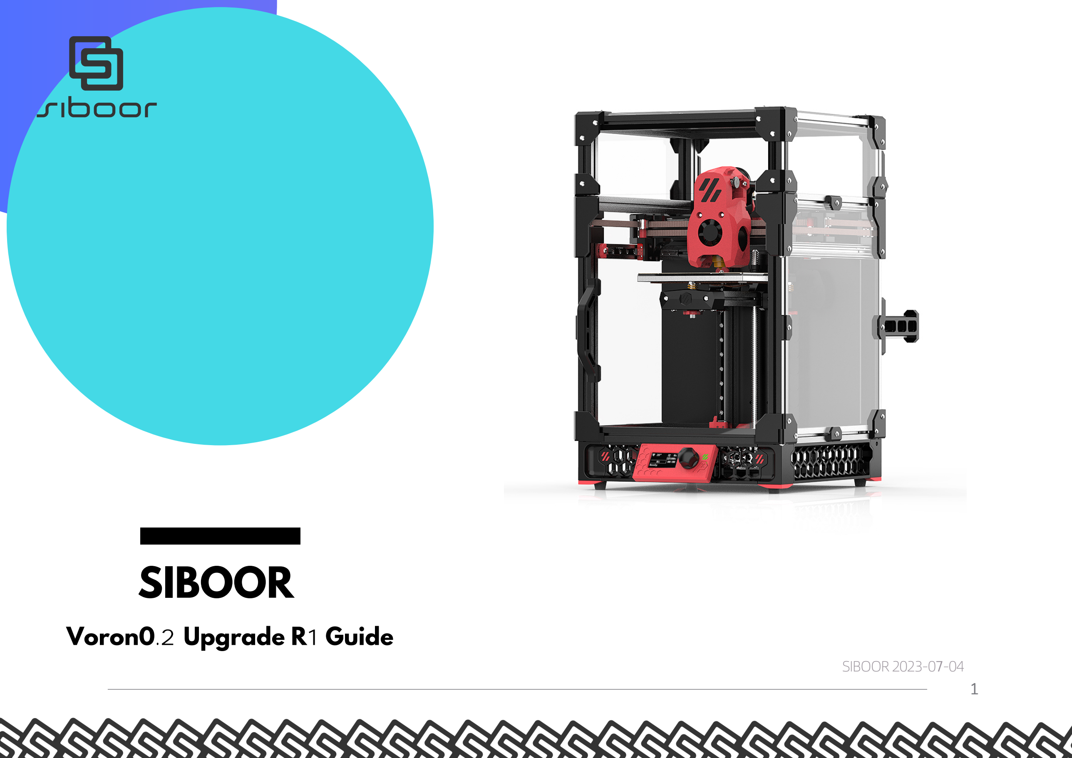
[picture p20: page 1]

1

SIBOOR 2023-0

7-04

# SIBOOR

## Voron0.2 Upgrade R

## 1 Guide

### INTRODUCTION

How to get help
How to find our SIBOOR community, where you can meet many SIBOOR 0.2 users like you
if anyone have any issues do not hesitate to reach out , we welcome suggestions or feedback and we are happy to face and overcome our challanges to improve our products.

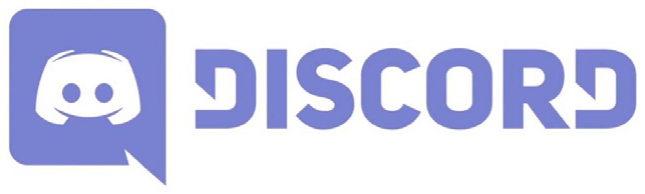
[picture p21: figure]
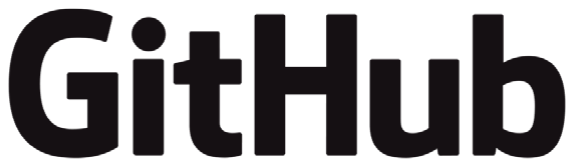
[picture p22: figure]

Voron design：https://www.vorondesign.com/

mellow Fly：https://mellow.klipper.cn/#/

klipper：https://www.klipper3d.org/zh/

Here you can view our database on GITHUB
https://github.com/Lzhikai/siboor-voron

2

https://discord.gg/hpF4bBbrht

### V0.2 R1 (2023 June)

① Skirts

-We fixed the issue where 34mm Z motors didnt fit in the machine with the bottom panel installed, this involved increasing the height of the skirts/ feet by 2mm
-We added a simple filament runout sensor to the rear right foot

② Toolhead

-Mini Stealthburner direct drive and bowden cowling part cooling ducts improved
-an issue with the guidler being able to pivot in an undesired direction was addressed by tightening the bolt holes to reduce play -RIDGA support for the bearings that come stock with the ridga kit has been added

③ Tophat

-cam locks for the tophat were changed to a simple hex key design

④ Z Endstop

-z endstop mount was beefed up to improve ridgidity

BOM Changes the BOM increased by the following items

-2x m2x10 self tapping screw
-1x MR85 bearing
-1x Microswitch
-1x ECAS04 Bowden Collet

https://github.com/VoronDesign/Voron-0

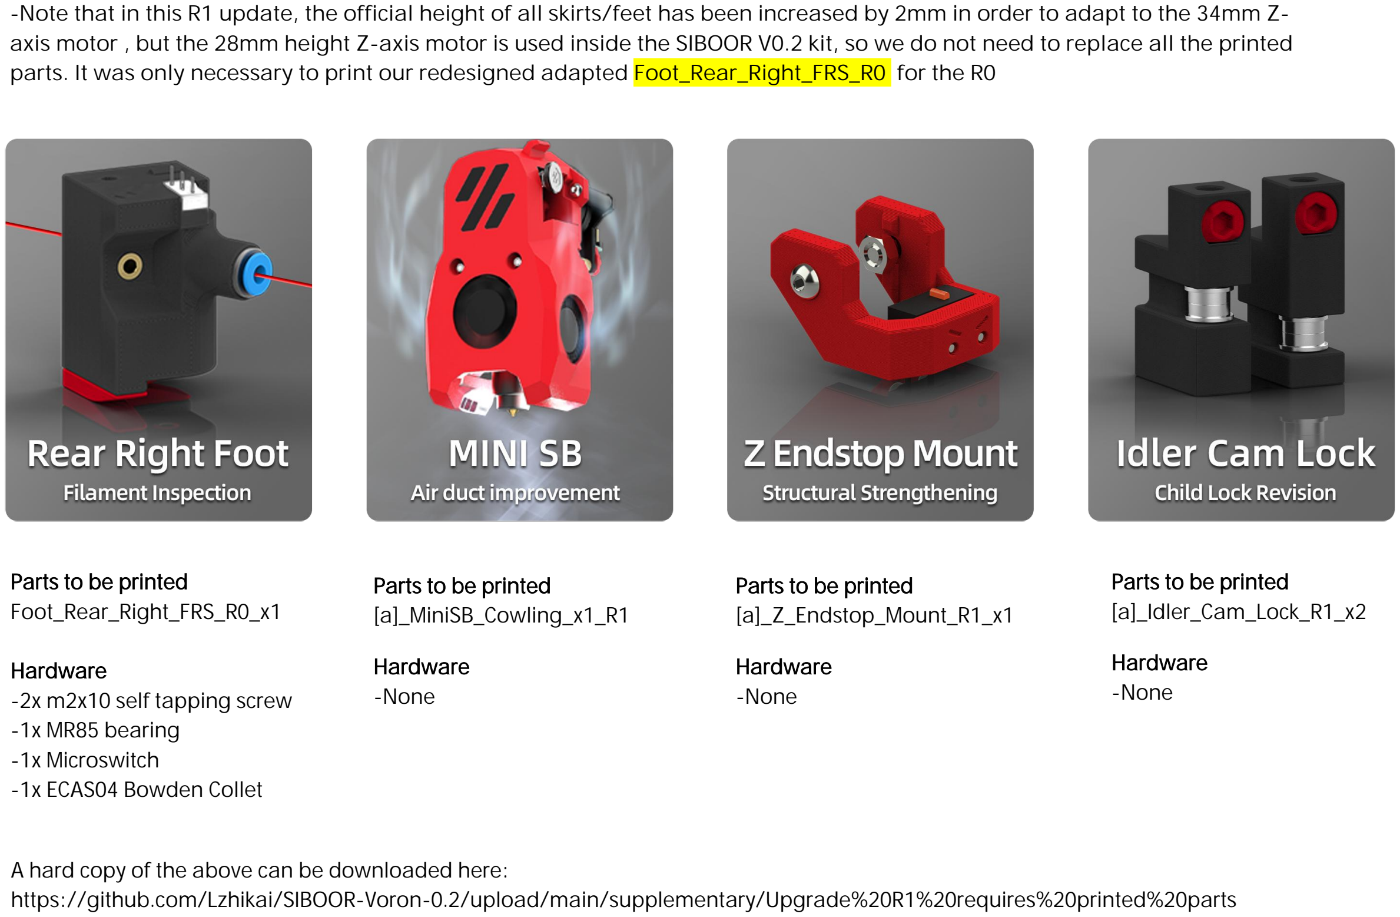
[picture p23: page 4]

-Note that in this R1 update, the official height of all skirts/feet has been increased by 2mm in order to adapt to the 34mm Z-axis motor , but the 28mm height Z-axis motor is used inside the SIBOOR V0.2 kit, so we do not need to replace all the printed parts. It was only necessary to print our redesigned adapted Foot_Rear_Right_FRS_R0 for the R0

Parts to be printed
Foot_Rear_Right_FRS_R0_x1

Hardware
-2x m2x10 self tapping screw -1x MR85 bearing
-1x Microswitch
-1x ECAS04 Bowden Collet

Parts to be printed
[a]_Idler_Cam_Lock_R1_x2

Hardware

Parts to be printed
[a]_Z_Endstop_Mount_R1_x1

Hardware

Parts to be printed
[a]_MiniSB_Cowling_x1_R1

Hardware
-None | -None | -None

A hard copy of the above can be downloaded here: https://github.com/Lzhikai/SIBOOR-Voron-0.2/upload/main/supplementary/Upgrade%20R1%20requires%20printed%20parts

# WHO ARE WE?

# INFINITE PURSUIT OF KNOWLEDGE

## in Chinese , the ultimate and infinite search of thought or knowledge this

is what Siboor stands for.

## We are on a continues pursuit of knowledge, thriving to perfect our products and offering and aim to bring in like minded pioneers into a forward motion towards innovation

and | to | speedup | technological

## advancement in the 3D printing

ecosystem..

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
UIDELINES | SIB

O

O

R

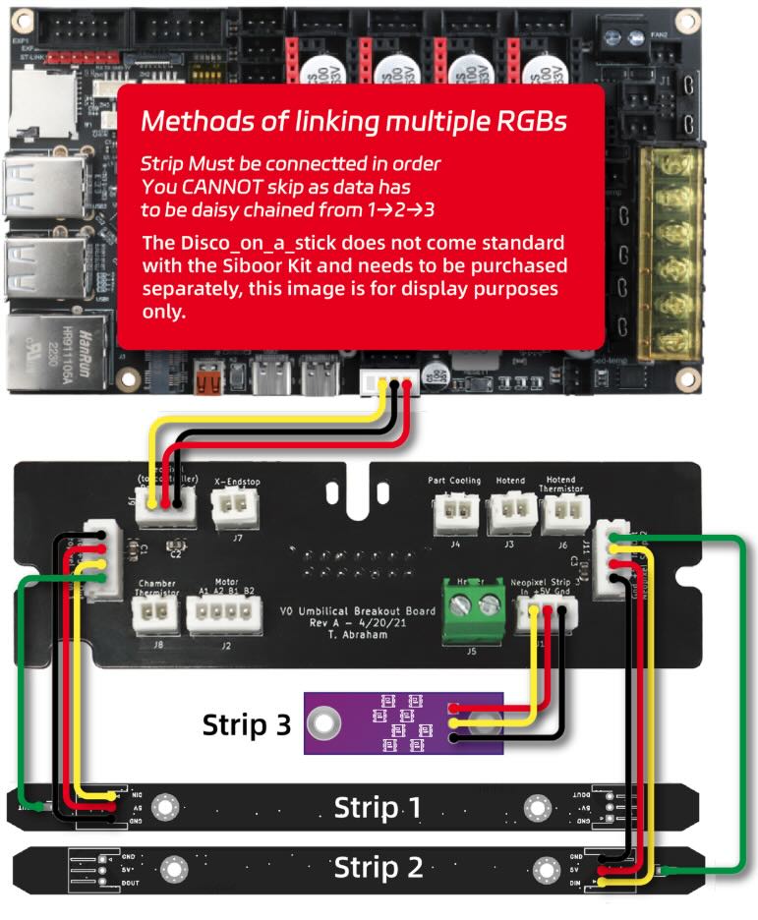
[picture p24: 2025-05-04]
images/02_LED_Wiring/Multiple_RGBs.jpg

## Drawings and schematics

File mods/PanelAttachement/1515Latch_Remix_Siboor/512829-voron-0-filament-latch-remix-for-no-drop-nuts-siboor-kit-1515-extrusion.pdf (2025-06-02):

## Voron 0 Filament

## latch Remix for no

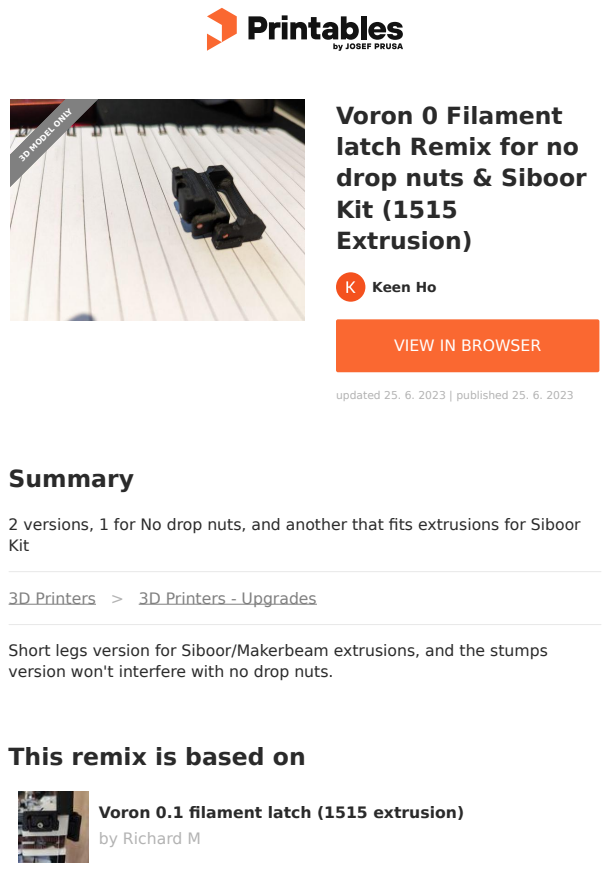
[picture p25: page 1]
Summary; Keen Ho; updated 25. 6. 2023 | published 25. 6. 2023; 3D MODEL ONLY

drop nuts & Siboor
Kit (1515
Extrusion)

VIEW IN BROWSER (https://printables.com/model/512829-voron-0-filament-latch-remix-for-no-drop-nuts-sibo)

2 versions, 1 for No drop nuts, and another that fits extrusions for Siboor
Kit

3D Printers (https://printables.com/model?categoryId=1) > 3D Printers - Upgrades (https://printables.com/model?categoryId=2)

Short legs version for Siboor/Makerbeam extrusions, and the stumps
version won't interfere with no drop nuts.

This remix is based on

Voron 0.1 filament latch (1515 extrusion) (https://printables.com/model/172427-voron-01-filament-latch-1515-extrusion)
by Richard M (https://printables.com/@RichardM)

## Model files

## License

This work is licensed under a
Creative Commons (4.0 International License)

Attribution (http://creativecommons.org/licenses/by/4.0/)

✖ | Sharing without ATTRIBUTION
✔ | Remix Culture allowed
✔ | Commercial Use
✔ | Free Cultural Works
✔ | Meets Open Definition

newlatch-v01-30mm-short-legs.stl

newlatch-v01-30mm-stumps.stl

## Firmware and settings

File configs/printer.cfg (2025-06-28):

# This lives in:
# Notes:
#   - This file lives on Voron at: /home/fly/printer_data/config/
#       - There are simlinked files around it:
#           - mainsail.cfg is a simlink to /home/fly/mainsail-config/client.cfg
#           - fluidd.cfg is a simlink to /home/fly/fluidd-config/client.cfg
#       - Other files referred to here are stored relative to this file. They are mainly helpers
#   - The origin is defined as:
#       - x - moves the toolhead left to right. 0 is LEFT  of bed. After Homing is set to: 110.
#       - y - moves the toolhead front to back. 0 is FRONT of bed. After Homing is set to: 110.
#       - z - moves the bed from top to bottom. 0 is TOP where want toolhead to be to print. After Homing is set to: 30 (for some clearance)
#           - As home is fixed from swtich we modify: position_endstop to ensure 0 is correct level for printing. See notes for [stepper_z].
#               - fly_macros.cfg overrides homing procedure allowing adjustments to positions
#       - This is consistent with directions of STEPPER_BUZZ command on https://docs.vorondesign.com/build/startup/#stepper-motor-check
#           - I originally had inverted z direction

[include mainsail.cfg]
[include fluidd.cfg]

[include fly_macros.cfg]
[include boards/FLY_GEMINI_V3.cfg]
[include V0Display.cfg]

[include led_effects.cfg]

[mcu]
serial: /dev/serial/by-id/usb-Klipper_stm32f405xx_28003D001547323330373434-if00

[mcu host]
serial: /tmp/klipper_host_mcu

[virtual_sdcard]
path: /home/fly/printer_data/gcodes
on_error_gcode: CANCEL_PRINT

[printer]
kinematics: corexy
max_velocity: 300
max_accel: 3000
max_z_velocity: 5
max_z_accel: 100


# Sensorless homnig wanted this: https://docs.vorondesign.com/tuning/sensorless.html
[force_move]
enable_force_move: True


########################################
# Temperature
########################################

[temperature_sensor FLY-Gemini]
sensor_type: temperature_host

[temperature_fan mcu_fan]       # Electrical bin cooling fan
pin: FAN1                   
kick_start_time: 0.500
sensor_type: temperature_mcu
control: watermark
target_temp: 45.0
min_temp: 0
max_temp: 90
max_speed: 1.0
min_speed: 0.8

########################################
# LED
########################################

# Note: The V0Display.cfg also defined [neopixel displayStatus]

# Initialize to ORANGE to indicate expect overridden by effect
# The effects are defined in led_effects.cfg
[neopixel bed_neopixel]
pin: NEOPIXEL_KIRIGAMI_BED
chain_count: 8
color_order: GRB
initial_RED: 0.2
initial_GREEN: 0.1
initial_BLUE: 0.0

# FUTURE: Add LEDs to toolhead and array to enclosure
#[output_pin HE-LED]
## This can be driven from klipper console with: SET_PIN PIN=HE-LED VALUE=1
## HOWEVER it did NOT appear to do anything -> MAYBE LED upgrade needs protol not simple high/low
##pin: PB1           # Matches wiring. Examples were host:gpio3 (Siboor) and !PB1 (Jjarrard)
#pin: host:gpio3
#pwm: False
##value: 0


########################################
# filament_switch_sensor
########################################

# FUTURE: Add filament runout sensor
# From example these were used; example (Jjarrard) was all commented out
#[filament_switch_sensor DLJC]
#pause_on_runout: True
## When set to True, a pause will be executed immediately after a material break
## , if False, a material break pause will not be enabled
#runout_gcode: PAUSE
## G-code to be executed after a material break
#insert_gcode: RESUME
## G-code to be executed after insertion of consumables
#event_delay: 3.0
## Minimum time delay between events, in seconds
#pause_delay: 0.5
## Delay between pause commands, scheduling and execution of runout_gcode in seconds
## , increasing delay if strange pause behaviour occurs
#switch_pin: !PB1

########################################
# Drives
########################################

## Refer to https://docs.vorondesign.com/build/startup/#v0
# Check motor direction in link above. If inverted, add/remove a band before dir_pin
[stepper_x]
step_pin: X_STEP
dir_pin: !X_DIR
enable_pin: !X_EN
rotation_distance: 40
microsteps: 16                                      # Examples were 16 (siboor), 32 (Jjarrard)
full_steps_per_rotation: 200                        # Set to 400 for 0.9° degree stepper motor, 200 is for 1.8° stepper motors
endstop_pin: tmc2209_stepper_x:virtual_endstop      # This is sensorless in my kit; no connection to X_STOP
position_endstop: 120
position_max: 120                                   # Note: In practice may only want to use to 117.
homing_speed: 30                                    # Advised can be increased after initial setup, Max 100. Original was 30
homing_retract_dist: 0
homing_positive_dir: true
step_pulse_duration: 0.000001                       # Examples were 0.000001 (siboor) and 0.000004 (Jjarrard)

[stepper_y]
step_pin: Y_STEP
dir_pin: !Y_DIR
enable_pin: !Y_EN
rotation_distance: 40
microsteps: 16                                      # Examples were 16 (siboor), 32 (Jjarrard)
full_steps_per_rotation: 200                        # Set to 400 for 0.9° degree stepper motor, 200 is for 1.8° stepper motors
endstop_pin: tmc2209_stepper_y:virtual_endstop      # This is sensorless in my kit; no connection to Y_STOP
position_endstop: 120
position_max: 120                                   # Note: In practice may only want to use to 117.
homing_speed: 30                                    # Advised can be increased after initial setup, Max 100. Original was 30
homing_retract_dist: 0
homing_positive_dir: true
step_pulse_duration: 0.000001                       # Examples were 0.000001 (siboor and Jjarrard)

[stepper_z]
# Note:
#   - The 0.2R1 kit has endstop at bottom of printer (away from toolhead) while earlier it was at the top - so careful comparing configs.
#   - This is setup so 120 is correct place place nozzle to print correctly.
#       - This could be removed with a z-probe; likely removing endstop on bottom.
#   - So the endstop (at bottom) will be the MINIMUM (think can go lower to help tune is being set).
#   - The hotend is then at 0 so always adjust these values for that to be true.
#   - I believe Klipper doesn't allow for max and min endstops (virtual or otherwise) which would be great here.
#   - To help with tuning we have position_min as -5.0 but don't expect to use negative.
#   - We need to calculate position_endstop for each toolhead/nozzle/bed:
#       - Use placeholder position_endstop value, say 115.0, load and do homing. Also allow position_min to have some additional tolerance.
#       - Use Z_ENDSTOP_CALIBRATE to have Manual Probe adjustments (TESTZ Z=...); accept. The log will then how eg position_endstop: 117.130. SAVE_CONFIG to write
#           - Can also do Z-Offset near homing section, then Z_OFFSET_APPLY_ENDSTOP but this had less precision.
#       - Klipper requires position_endstop to be between position_min and position_max
#           - position_max was then set to be 0.5 more than the z-offset - allows printing but would trigger switch.
#   - The position_endstop is POTENTIALLY commented out when going through tunign and saving file.
step_pin: Z_STEP
dir_pin: !Z_DIR                                     # This is set for correct buzz direction
enable_pin: !Z_EN
rotation_distance: 8                                # For T8x8 integrated lead screw
microsteps: 16                                      # Examples were 16 and 32
endstop_pin: Z_STOP                                 # The 0.2R1 kit moved to bottom. In future look at something to level extruder to bed.
#endstop_pin: tmc2240_stepper_z:virtual_endstop     # FUTURE: See if can do do sensorless homing to hit extruder.
position_min: -5.0                                  # Want set to 0 for printing to have nozzel at correct height. Have some additional height for tuning. For new toolheads/nozzle/bed decrease for tolerance.
# In future may need to select appropriate based on build plate, hotend and nozzel.
#position_endstop: 116.560                          # Z_ENDSTOP_CALIBRATE stores at bottom. This is PEI Sheet, 2nd Dragon HF with Stainless Steel nozzel (0.4mm) (at PLA temp)
position_max: 125.00                                # Set to at least 0.5 less than position_endstop to ensure in range.
homing_speed: 120                                   # Originally was 30; maybe can change after happy with setup. Example was 120 (siboor).
second_homing_speed: 3.0                            # This was in Siboor
homing_retract_dist: 3.0                            # This was in Siboor
homing_positive_dir: true                           # Want to home to positive so toolhead print location can be defined as 0.
#step_pulse_duration: 0.000001
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

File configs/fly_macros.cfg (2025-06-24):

# Note:
#   These show up in the Klipper WebUI with other Macros
#   These are case insensitive.

# The klipper screen had these but didn't see where set - may have different values.
# These are defined to allow using via WebUI
[gcode_macro Preheat_PLA]
description: Preheat for PLA printing
gcode:
    {% set extruder_temp = params.EXTRUDER_TEMP|default(200) %} # Default to 200°C
    {% set bed_temp = params.BED_TEMP|default(60) %}            # Default to 60°C
    M109 S{extruder_temp}   ; Set extruder temperature and wait
    M190 S{bed_temp}       ; Set bed temperature, don't wait. Use M190 if want to wait or M140 if happy to continue.

[gcode_macro Preheat_PETG]
description: Preheat for PETG printing
gcode:
    {% set extruder_temp = params.EXTRUDER_TEMP|default(240) %} # Default to 240°C
    {% set bed_temp = params.BED_TEMP|default(80) %}            # Default to 80°C
    M109 S{extruder_temp}   ; Set extruder temperature and wait
    M190 S{bed_temp}       ; Set bed temperature, don't wait. Use M190 if want to wait or M140 if happy to continue.

[gcode_macro Preheat_ABS]
description: Preheat for ABS printing
gcode:
    {% set extruder_temp = params.EXTRUDER_TEMP|default(240) %} # Default to 240°C
    {% set bed_temp = params.BED_TEMP|default(110) %}            # Default to 110°C
    M109 S{extruder_temp}   ; Set extruder temperature and wait
    M190 S{bed_temp}       ; Set bed temperature, don't wait. Use M190 if want to wait or M140 if happy to continue.

[gcode_macro SHUTDOWN]
gcode:
  {action_call_remote_method("shutdown_machine")}

[pause_resume]

[display_status]

[gcode_macro CANCEL_PRINT]
rename_existing: BASE_CANCEL_PRINT
gcode:
    TURN_OFF_HEATERS
    CLEAR_PAUSE
    SDCARD_RESET_FILE
    BASE_CANCEL_PRINT

[gcode_macro PAUSE]
rename_existing: BASE_PAUSE
gcode:
    ##### set defaults #####
    {% set x = params.X|default(230) %}      #edit to your park position
    {% set y = params.Y|default(230) %}      #edit to your park position
    {% set z = params.Z|default(10)|float %} #edit to your park position
    {% set e = params.E|default(1) %}        #edit to your retract length
    ##### calculate save lift position #####
    {% set max_z = printer.toolhead.axis_maximum.z|float %}
    {% set act_z = printer.toolhead.position.z|float %}
    {% set lift_z = z|abs %}
    {% if act_z < (max_z - lift_z) %}
        {% set z_safe = lift_z %}
    {% else %}
        {% set z_safe = max_z - act_z %}
    {% endif %}
    ##### end of definitions #####
    SAVE_GCODE_STATE NAME=PAUSE_state
    BASE_PAUSE
    G91
    G1 E-{e} F2100
    G1 Z{z_safe}
    G90
    G1 X{x} Y{y} F6000


[gcode_macro RESUME]
rename_existing: BASE_RESUME
gcode:
    ##### set defaults #####
    {% set e = params.E|default(1) %} #edit to your retract length
    G91
    G1 E{e} F2100
    G90
    RESTORE_GCODE_STATE NAME=PAUSE_state MOVE=1
    BASE_RESUME


[homing_override]
axes: xyz
# set_position_z: 20  ; Was originally 0, tried changing to 20 but would NOT allow moving down before homing.
gcode:
   G90              ; absolute positioning
   ;G0 Z-5 F600      ; Was originally G0 Z5 F600 - Issues moving down saying out of bounds before homed (G0 Z-5 F600)
  {% set home_all = 'X' not in params and 'Y' not in params and 'Z' not in params %}

  {% if home_all or 'X' in params %}
    _HOME_X
  {% endif %}
  
  {% if home_all or 'Y' in params %}
    _HOME_Y
  {% endif %}
  
  {% if home_all or 'Z' in params %}
    _HOME_Z
  {% endif %}

  LED_HOMED         ; Trigger LED gcode macro to indicate finished homing

# Requires [bed_screws] or [screws_tilt_adjust] to be defiend for macros to run see https://klipperscreen.readthedocs.io/en/latest/Panels/Screws/
# See https://www.klipper3d.org/Config_Reference.html#bed_screws
# Think these values are used by;  /home/fly//klipper/klippy/extras/bed_screws.py
[bed_screws]
screw1: 60,5
screw1_name: front screw
screw2: 5,115
screw2_name: back left
screw3: 115,115
screw3_name: back right
Probe_height: 0.1
#horizontal_move_z: 5
#   The height (in mm) that the head should be commanded to move to
#   when moving from one screw location to the next. The default is 5.
#probe_height: 0
#   The height of the probe (in mm) after adjusting for the thermal
#   expansion of bed and nozzle. The default is zero.
#speed: 50
#   The speed (in mm/s) of non-probing moves during the calibration.
#   The default is 50.
#probe_speed: 5
#   The speed (in mm/s) when moving from a horizontal_move_z position
#   to a probe_height position. The default is 5.

[gcode_macro LOAD_FILAMENT]
gcode:
   M83                            ; set extruder to relative
   G1 E30 F300                    ; load
   G1 E15 F150                    ; prime nozzle with filament
   M82                            ; set extruder to absolute
    
[gcode_macro UNLOAD_FILAMENT]
gcode:
   M83                            ; set extruder to relative
   G1 E10 F300                    ; extrude a little to soften tip
   G1 E-40 F1800                  ; retract some, but not too much or it will jam
   M82                            ; set extruder to absolute

[gcode_macro _HOME_X]
gcode:
    # Always use consistent run_current on A/B steppers during sensorless homing
    {% set RUN_CURRENT_X = printer.configfile.settings['tmc2209 stepper_x'].run_current|float %}
    {% set RUN_CURRENT_Y = printer.configfile.settings['tmc2209 stepper_y'].run_current|float %}
    {% set HOME_CURRENT = 0.7 %}
    SET_TMC_CURRENT STEPPER=stepper_x CURRENT={HOME_CURRENT}
    SET_TMC_CURRENT STEPPER=stepper_y CURRENT={HOME_CURRENT}

    M400            ; Clear any commands - including stallguards.
    # Home - If issues we MAY want to tell it to assume an initial position, SET_KINEMATIC_POSITION X=15
    G28 X           ; home x
    # Move away
    G91             ; relative positioning
    G1 X-10 F1200   ; Move back from limit
    
    # Wait just a second… (give StallGuard registers time to clear)
    G4 P1000        ; pause for x ms
    G90             ; absolute positioning

    G1 X60          ; Set to middle of plate

    # Restore the full current for printing
    SET_TMC_CURRENT STEPPER=stepper_x CURRENT={RUN_CURRENT_X}
    SET_TMC_CURRENT STEPPER=stepper_y CURRENT={RUN_CURRENT_Y}

[gcode_macro _HOME_Y]
gcode:
    # Set current for sensorless homing
    {% set RUN_CURRENT_X = printer.configfile.settings['tmc2209 stepper_x'].run_current|float %}
    {% set RUN_CURRENT_Y = printer.configfile.settings['tmc2209 stepper_y'].run_current|float %}
    {% set HOME_CURRENT = 0.7 %}
    SET_TMC_CURRENT STEPPER=stepper_x CURRENT={HOME_CURRENT}
    SET_TMC_CURRENT STEPPER=stepper_y CURRENT={HOME_CURRENT}

    M400            ; Clear any commands - including stallguards.
    # Home - If issues we MAY want to tell it to assume an initial position, SET_KINEMATIC_POSITION Y=15
    G28 Y           ; home x
    # Move away
    G91             ; relative positioning
    G1 Y-10 F1200   ; Move back from limit

    # Wait just a second… (give StallGuard registers time to clear)
    G4 P1000    ; pause for x ms
    G90         ; absolute positioning

    G1 Y60      ; Set to middle of plate

    # Restore the full current for printing
    SET_TMC_CURRENT STEPPER=stepper_x CURRENT={RUN_CURRENT_X}
    SET_TMC_CURRENT STEPPER=stepper_y CURRENT={RUN_CURRENT_Y}


[gcode_macro _HOME_Z]
gcode:
    G90         ; absolute positioning
    G28 Z       ; home z
    G1 Z30      ; position to end up with some space until toolhead
################################################################################
################################################################################

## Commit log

2025-04-09 Snapshot of current configs
    [FLY_GEMINI_V3.cfg, V0Display.cfg, fly_macros.cfg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]
2025-04-26 Fixed clog in extruder
2025-04-27 Made an niitial led_effects file. Included initial effects
    [FLY_GEMINI_V3.cfg, V0Display.cfg, led_effects.cfg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]
2025-04-27 Added LEDS for bed temp, hotend temp, homed, idle and finished
    [V0Display.cfg, VORON 0 carrying handles.stl, VORON v0.0_v0.1_legacy_chain_mount.stl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]
2025-05-01 Fixed assembly build notes and made markdown. Added more parts I purchased
2025-05-01 Redid PIP tuning
    [printer.cfg]
2025-05-01 Added sample files
    [printer-20250331_001844.cfg, printer-20250331_002800.cfg, printer-20250331_032819.cfg]
2025-05-01 Cleaned macros while looking at bed_adjust
    [FLY_GEMINI_V3.cfg, fly_macros.cfg, led_effects.cfg]
2025-05-01 Redid PID tuning with silicon cover. Updated some notes in config
    [printer.cfg]
2025-05-01 Tuned sensorless homing. Added to cura
    [printer.cfg]
2025-05-01 Fixed PIDs after warnings on load
    [printer.cfg]
2025-05-01 Looked at all sensorless homing and minor update due to x reliability
    [fly_macros.cfg, printer.cfg]
2025-05-03 Fixed z-axis direction and homing. Now homes at sets to middle of plate 30cm below toolhead
    [fly_macros.cfg, printer.cfg]
2025-05-03 Z tuning for PEI temps; 200/60
    [printer.cfg]
2025-05-03 Added Voron bed texture Updated start macro with correct z direction
    [printer.cfg]
2025-05-04 Added some useful STLs and info on current system
    [Brackets_1515_x2.step, Brackets_1515_x2.stl, Brackets_2020.step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]
2025-05-06 Added notes on leveling/probe
2025-06-02 Some mode cleanup
    [NewLatch-v0.1-3.0mm-short-legs.stl, NewLatch-v0.1-3.0mm-stumps.stl, VORON 0 carrying handles.stl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]
2025-06-02 Bumped temp to avoid crash
    [printer.cfg]
2025-06-02 Added new USB camera. Not yet mounted so may need to rotate
2025-06-24 Added Preheat macros to drive from GUI
    [fly_macros.cfg]
2025-06-28 Added mount for Phaetus Dragon HF - got second to swap blocks quicker
    [FS_Hotend_Mount_Dragon.stl]
2025-06-28 Tuned with 2nd dragon HF after blockage
    [printer.cfg]
